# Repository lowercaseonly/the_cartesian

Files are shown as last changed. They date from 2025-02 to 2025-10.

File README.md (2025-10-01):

# The Cartesian
**The Cartesian** is a modular CNC Mill built from low-cost standard parts (which can ve bought of the shelf) as well as 3D-printed connectors.

## Folder Structure

```
.
│   README.md                      # This File
│   bom.csv                        # Bill of Materials
└───3d_models                      # Hardware 3D Models
│   └───assembly                   # Compositions of Components
│   │   │   parameter.scad         # Global Assembly Parameters
│   │   │   portal_assembly.scad   # X-Axis
│   │   │   bridge_assembly.scad   # Y-Axis
│   │   │   column_assembly.scad   # Z-Axis
│   │   │   assembly.scad          # Overall Assembly
│   └───helper                     # Helper Models (Shared between different Machine Parts)
│   │   ...
│   └───components                 # Printable Component Models
│   │   ...
│   └───shells                     # off-the-shelf Component Models
│       ...
└───src                            # Source Code
```

## Mechanical Setup
The basic mechnical structure of the described hardware consists of three linear axis which are oriented orthogonal to each other (hence the project name).

### General Considerations
The hardware is based on standard parts around which customized connectors are built. The exact bill of materials can be found in a dedicated file in the root directory of this repository and includes:

 - `NUT8` aluminum profiles (more about [T-Slot structural Framing](https://en.wikipedia.org/wiki/T-slot_structural_framing))
 - `M5` screws and nuts (more about [metric screws](https://en.wikipedia.org/wiki/ISO_metric_screw_thread))
 - `HGH20` linear guide blocks and rails (more about [HIWIN](https://www.hiwin.tw/))
 - `NEMA 23` stepper motors (more about the [NEMA](https://www.nema.org/Standards/view/Motion-Position-Control-Motors-Controls-and-Feedback-Devices) Standard)

### Design Principles
The hardware of this project is designed adhering to some basic principles:

 - The 3D Models are given as [OpenSCAD](https://openscad.org/) Files
 - All numerical values in the 3D model files are given in [mm](https://en.wikipedia.org/wiki/Millimetre)
 - Parametrization is used whenever possible. For example, the exact printing area can be specified by three individual parameters
 - A [tagging function](./3d_models/helper/bom.scad) is used in all component functions to generate the bill of material automatically

### Overall Assembly
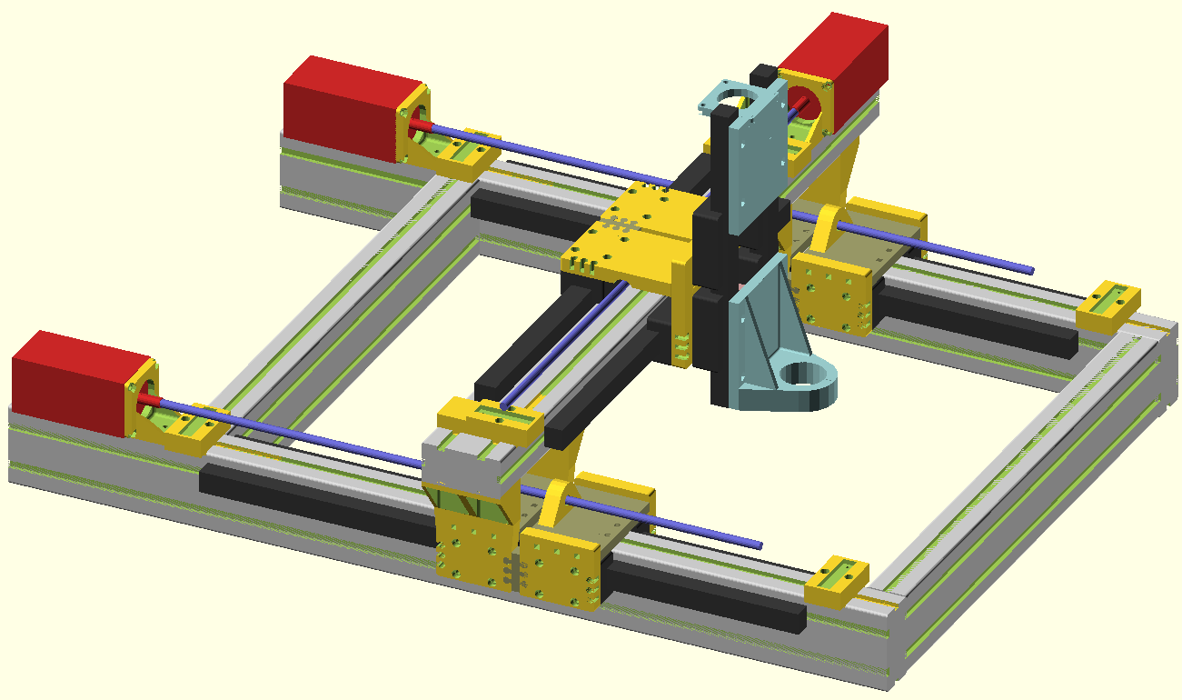
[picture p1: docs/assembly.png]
Overall Assembly

In order to validate the designs of individual components as well as for simulation and illustration purposes, the assembly of the overall machine has been created aggregating the models of individual (printable and off-the-shelf) components. All assembly files can be found in the [3d_models/assembly](./3d_models/assembly) folder. More precisely:

 - The overall [assembly.scad](./3d_models/assembly/assembly.scad) file utilizes the individual axis assemblies by geometrically linking them (using OpenSCAD's `children()` transform).
 - The assembly parameters are stored globally in [parameter.scad](./3d_models/assembly/parameter.scad). Here, multiple aspects can be adjusted:
   - The individual axis dimensions: `SPACE_X`, `SPACE_Y`, `SPACE_Z`
   - The end effector position: `POS_X`, `POS_Y`, `POS_Z`

### The Portal (X-Axis)
The X-Axis (also referred to as `portal`) consists of the main structural, rectangular frame build from T-slotted (aluminum) profiles. On this frame, two pairs of linear guide rails are mounted which commonly carry another T-slotted profile (the bridge). Each pair of guide rails is driven by a dedicated motor.

### The Bridge (Y-Axis)
The Y-Axis (also referred to as `bridge`) consists of a one T-slotted profile on which two two linear guild rails are mounted. The bridge is driven by one motor which is mounted to two T-Slots.

### The Column (Z-Axis)
The Z-Axis (also referred to as `column`) consists of a plate, mounted to two linear guide rails that carries the end-effector.

## License
The content of this repository is licensed under the terms of the `MIT license`.

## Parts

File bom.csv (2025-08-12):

BOM Level | Description | Part Number | Unit Cost | Quantity | Total Cost
 | T-Slot Profile [Type Nut8, 40x2, length: 1200mm] |  |  | 2
 | T-Nut |  |  | 20
 | Profile Angle |  |  | 20
 | M-Skrew

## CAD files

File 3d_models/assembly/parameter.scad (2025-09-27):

/*
  Author: Johannes Bayer, 2025
  License: MIT
  Description: Global Assembly Parameters
*/


REINFORCEMENT = true;
PORTAL_SPACING = 8;
BRIDGE_SPACING = 7;
COLUMN_SPACING = 10;

MOTOR_SPACE=200;

// Printing Area
SPACE_X = 600;
SPACE_Y = 600;
SPACE_Z = 300;
PORTAL_HEIGHT = 110; // TODO resolve by SPACE_Z based Formula

// Printer Head Position
POS_X = 250;
POS_Y = 200;
POS_Z = 100; // 110/300: [65-135]

// Counter Axis (Slider/Profile/Component) Dimensions
OFFSET_Y = 90;

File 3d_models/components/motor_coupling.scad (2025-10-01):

include <../helper/bom.scad>

include <../shells/motor.scad>
include <../shells/threaded_rod.scad>



MOTOR_COUPLING_DIA = 20;
MOTOR_COUPLING_LEN = 20;
MOTOR_COUPLING_ROD_ATTACH = 10.0;
MOTOR_COUPLING_SHAFT_ATTACH = 5.0;



module motor_coupling(){

    bom_item("MOTOR_COUPLING");

    difference(){

        translate([0,0,-MOTOR_COUPLING_SHAFT_ATTACH])
            cylinder(h=MOTOR_COUPLING_LEN,d=MOTOR_COUPLING_DIA);

        union(){

            translate([0,0,-MOTOR_SHAFT_LEN-MOTOR_CON_LEN])
                motor_shaft();
            translate([0,0,MOTOR_COUPLING_LEN-MOTOR_COUPLING_SHAFT_ATTACH
                           -MOTOR_COUPLING_ROD_ATTACH+NOTHING])
                cylinder(h=MOTOR_COUPLING_ROD_ATTACH, d=THEADED_ROD_DIA_OUTER);

        }

    }

    translate([0,0,MOTOR_COUPLING_LEN-MOTOR_COUPLING_SHAFT_ATTACH
                   -MOTOR_COUPLING_ROD_ATTACH+NOTHING])
        children();

}


motor_coupling($fn=400);

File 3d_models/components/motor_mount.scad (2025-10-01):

include <../helper/bom.scad>
include <../helper/motor_flange.scad>
include <../helper/t_slot.scad>


MOTOR_MOUNT_THICKNESS = 25.0;
MOTOR_MOUNT_LENGTH = 5.0;
MOTOR_MOUNT_LEFT = true;



module motor_mount(double_t_slot=false){

    bom_item("MOTOR_MOUNT",
             "T-SLOT_TYPE",double_t_slot?"double":"single");

    translate([0,0,MOTOR_FLANGE_HEIGHT/2])
        rotate([90,0,180])
            motor_flange()
                children();

    difference(){
        translate([SLOT_PROF_HEIGHT/2
                   +(double_t_slot&&MOTOR_MOUNT_LEFT?SLOT_DIST+SLOT_WIDTH:0),0,0])
            rotate([-90,90,0])
                NUT8_mount(length=MOTOR_MOUNT_THICKNESS,
                           thickness_length=MOTOR_MOUNT_LENGTH,
                           thickness_height=MOTOR_FLANGE_THICKNESS,
                           double_size=double_t_slot);
        translate([0,0,MOTOR_FLANGE_HEIGHT/2])
            rotate([90,0,180])
                motor_flange_cutout();
    };

}

motor_mount($fn=100, double_t_slot=false);

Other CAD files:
3d_models/helper/motor_flange.scad
3d_models/assembly/assembly.scad
3d_models/assembly/bridge_assembly.scad
3d_models/assembly/column_assembly.scad
3d_models/assembly/portal_assembly.scad
3d_models/components/bearing_mount.scad
3d_models/components/bridge.scad
3d_models/components/bridge_compact.scad
3d_models/components/bridge_connector.scad
3d_models/components/bridge_reinforcement.scad
3d_models/components/column.scad
3d_models/components/column_connector.scad
3d_models/components/nut_mount.scad
3d_models/components/portal.scad
3d_models/components/portal_reinforcement.scad
3d_models/components/thread_nut_mount.scad
3d_models/components/wagon_connector.scad
3d_models/helper/base_plate.scad
3d_models/helper/bom.scad
3d_models/helper/connector_a.scad
3d_models/helper/linear_wagon.scad
3d_models/helper/nut_mount_connector.scad
3d_models/helper/pillow_block.scad
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

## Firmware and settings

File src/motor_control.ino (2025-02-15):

int counter = 0;

void setup() {
  // put your setup code here, to run once:
  DDRD = 0b11111111;
  counter = 0;
}

void loop() {
  // put your main code here, to run repeatedly:

  delay(1);
  PORTD |= 0b00000001;
  delay(1);
  PORTD &= 0b11111110;
  counter++;

  if (counter%500==0)
    PORTD |= 0b00000010;
  if (counter%1000==0)
    PORTD &= 0b11111101;

}

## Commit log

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2025-06-08 Added First Draft of Linear Wagon Adapter for Portal
    [portal.scad]
2025-07-12 Added Connector to Portal
    [portal.scad]
2025-07-19 Added NUT8_45x2 Prototype Model
    [portal.scad]
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2025-07-21 Added T-Slot Profile connector
    [portal.scad]
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2025-07-22 Corrected Nut8 Mount Extrusion height
    [portal.scad]
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2025-07-22 Cleaned up Module Assembly
    [portal.scad]
2025-07-22 Corrected T-Slot Profile Parameters
    [portal.scad]
2025-07-22 Added Spindle Connector to Bridge
    [portal.scad]
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2025-07-22 Shrinked T-Slut Support to save Space and Material
    [portal.scad]
2025-07-22 Increased Circle Detail Rendering Parameter
    [portal.scad]
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2025-07-26 Fine-Tuned M-Skrew Drill Hole Sizes
    [portal.scad]
2025-08-02 Added Motor Flange Dimensions to Prepare Mount
    [motor_mount.scad]
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2025-08-02 Moved base_plate() Helper Function to Dedicated File
    [base_plate.scad, portal.scad]
2025-08-02 Moved m_skrew() Helper Function to Dedicated File
    [m_skrew.scad, portal.scad]
2025-08-02 Fixed Skrew Model Import
    [m_skrew.scad, portal.scad]
2025-08-02 Added Fist Version of motor_flange()
    [motor_mount.scad]
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2025-08-07 Moved Linear Wagon Helper Function to Dedicated File
    [linear_wagon.scad, portal.scad]
2025-08-07 Fixed Import in Motor Mount
    [motor_mount.scad]
2025-08-07 Fixed Import Structure in 3D Models
    [linear_wagon.scad, portal.scad]
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2025-08-10 Added and Improved Header Documentation in Helper Models
    [connector_a.scad, linear_wagon.scad]
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2025-08-10 Avoided Numerical Issues in NUT8_mount_complete()
    [t_slot.scad]
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2025-08-10 Reworked Parameters in NUT8_mount_complete() and NUT8_mount()
    [t_slot.scad]
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2025-08-11 Corrected Hole-Edge Distance in Motor Mount
    [motor_mount.scad]
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2025-08-12 Moved and Renamed Spindle Connector -> Nut Mount Connector to Dedicated Helper File
    [nut_mount_connector.scad, portal.scad]
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2025-08-12 Added Portal Reinforcement Component
    [portal_reinforcement.scad]
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2025-08-13 Addedd top, bottom, left, right Parameters to HGH20CA_screws()
    [linear_wagon.scad]
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2025-08-27 Clipped Nut Connector Mount as Makeshift to fit Small Printing Area in
    [nut_mount.scad]
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2025-08-27 Optimized Default Value of length Parameter in m_skrew_eject()
    [m_skrew.scad]
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2025-08-28 Fine-Tuned Tolerances in Nut Mount
    [nut_mount.scad, nut_mount_connector.scad]
2025-08-28 Fixed Wagon-Wagon Alignment in bridge_mount()
    [bridge_mount.scad]
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2025-08-31 Fixed m_nut()
    [m_skrew.scad]
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2025-09-01 Flipped Motor Flange in Motor Mount
    [motor_mount.scad]
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2025-09-01 Utilized motor_flange_cutout() in Motor Mount for Improved Nut Fitting
    [motor_mount.scad]
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2025-09-02 45 Degree Angle of Nut Holes in Motor Flange
    [motor_flange.scad]
2025-09-04 Fully Parameterized NUT8_mount() by introducing dedicated, independent Thicknesses
    [t_slot.scad]
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2025-09-07 Renamed bridge() -> intermediate() to Avoid Naming Ambiguities
    [portal.scad]
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2025-09-08 Replaced Redundant PORTAL_SPACING Parameter by Calculation
    [portal.scad]
2025-09-08 First Version of Bridge Reinforcement
    [bridge_reinforcement.scad]
2025-09-08 Properly Parameterized Nut Mount Connector in Bridge Reinforcement
    [bridge_reinforcement.scad]
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2025-09-08 Adapted Motor Mount to new T-Slot Mount Definition
    [motor_mount.scad]
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2025-09-09 Added Crossbars and Prepared Base Frame for Motor Mount
    [assembly.scad]
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2025-09-09 Added Reinforcement Option to Bridge Core
    [bridge.scad]
2025-09-09 Added Bridge Reinforcement to Assembly
    [assembly.scad]
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2025-09-09 Added Portal Reinforcement to Assembly
    [assembly.scad]
2025-09-10 Shortened Bridge to fit Small Printing Area
    [bridge.scad]
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2025-09-10 Moved set Arc Segment Variable from Global Definition to Main Function Call in all Components
    [bridge.scad, bridge_reinforcement.scad, motor_mount.scad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]
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2025-09-12 Added Default Value to extend Parameter in m_skrew()
    [m_skrew.scad]
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2025-09-12 Applied MOTOR_SPACE Variable to Bridge T-Slot Profile in Assembl
    [assembly.scad]
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2025-09-13 Replaced effector_mount() by pillow_block() Utilization in Column
    [column.scad]
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2025-09-14 Added Plane Crop to pillow_block() to Support center_dist Values Smaller than diameter and wall thickness sum
    [pillow_block.scad]
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2025-09-16 Added Functionality for Generating the Bill of Material Automatically
    [assembly.scad, bearing_mount.scad, bom.scad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]
2025-09-16 Added linear_slider() module combining HGH20() and HGH20CA() with coordinate Transform
    [linear_wagon.scad]
2025-09-16 Moved to Main Module Call in Nut Mount
    [nut_mount.scad]
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2025-09-16 Added Bridge Motor and Motor Mount to Assembly
    [assembly.scad]
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2025-09-17 Cleanup and Introduction of OFFSET_Y Parameter and Double T-Slot Bearing Mounts for Bridge in Assembly
    [assembly.scad]
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2025-09-17 Increased Safety Margin of Bearing Mount in Column
    [column.scad]
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2025-09-18 Redefined Linear Wagon and Slider to Center at Origin
    [linear_wagon.scad]
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2025-09-18 Adapted Motor Flange to new Base Plate Definition
    [motor_flange.scad]
2025-09-18 Adapted Motor Mount to Definition of Motor Flange
    [motor_mount.scad]
2025-09-18 Fixed overhang in HGH20CA_plate()
    [linear_wagon.scad]
2025-09-18 Adapted Portal Reinforcement to new Base Plate Definition
    [portal_reinforcement.scad]
2025-09-19 Adapted Bridge Reinforcement to new Base Plate Definition
    [bridge.scad]
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2025-09-19 Added Portal Reinforcement Symmetrically to Assembly
    [assembly.scad]
2025-09-19 Added Bridge including Reinforcement Symmetrically to Assembly
    [assembly.scad]
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2025-09-19 Parametrization and Adaptation to new Wagon Connector Definition in Assembly
    [assembly.scad]
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2025-09-19 Introduced invert Flag in linear_slider()
    [linear_wagon.scad]
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2025-09-19 Renamed NUT8_mount_base() -> support_base() and Moved to Dedicated File
    [support.scad, t_slot.scad]
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2025-09-19 Fixed Couout Alignment in support()
    [support.scad]
2025-09-19 Re-Implemented Column Support Structure to Avoid Numerical Issues
    [column.scad]
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2025-09-20 Renamed column() -> column_lower() and Encapsulated Overall column() Function
    [column.scad]
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2025-09-20 Introduced Margins to Fix Rendering for Zero-Thick Base in Support Structure
    [support.scad]
2025-09-20 Simplified Column Code by Applying Support Structure Fix
    [column.scad]
2025-09-20 Added Support Structure to Bearing Mount in Column
    [column.scad]
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2025-09-21 Aligned Nut Mount with Connector Base in Colomn Connector
    [column_connector.scad]
2025-09-21 Corrected Nut Length in Column Mount
    [column_connector.scad]
2025-09-21 Added Fitting Marging to Nut Mount in Column Connector
    [column_connector.scad]
2025-09-21 Decreased Column Connector Height to Avoid Collision with Main Column
    [column_connector.scad]
2025-09-21 Decreased Column Connector Width to Avoid Collision with Column Sliders
    [column_connector.scad]
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2025-09-21 Finetunig in Column Bearing Mount Support to Avoid Collision with Linear Sliders
    [column.scad]
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2025-09-22 Fixed Column Connector Position in Assembly
    [assembly.scad]
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2025-09-24 Fixed Children Transform in Bridge
    [bridge.scad]
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2025-09-25 Moved portal_assembly(), bridge_assembly() and column_assembly() to Dedicated Files
    [assembly.scad, bridge_assembly.scad, column_assembly.scad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]
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2025-09-25 Fixed Overall Assembly File
    [assembly.scad]
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2025-09-25 Replaced Redundant Union Operators
    [column.scad, connector_a.scad, motor_flange.scad]
2025-09-25 Added Missing Nut Mount Instances to Portal
    [portal_assembly.scad]
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2025-09-26 Adapted Portal Assembly to new Nut Mount Alignment
    [portal_assembly.scad]
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2025-09-27 Replaced Usage of motor() with motor_shaft() in motor_coupling()
    [motor_coupling.scad]
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2025-09-27 Fixed Parameters in Motor Coupling
    [motor_coupling.scad]
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2025-09-27 Fixed Cildren Transform in Motor Coupling
    [motor_coupling.scad]
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2025-09-27 Shortened Motor Coupling
    [motor_coupling.scad]
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2025-09-27 Decreased Outer Diameter in Motor Coupling to fit into Tight Mounting Space
    [motor_coupling.scad]
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2025-09-28 Added Brdige Connector and Nut Mount to Bridge Assembly
    [bridge_assembly.scad]
2025-09-28 Finetuning in Bridge Reinforcement
    [bridge_reinforcement.scad]
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2025-09-30 Added Motor Flange Support Structure to Upper Column Plate
    [column.scad]
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2025-09-30 Utilized Motor Flange Children Transform in Motor Mount
    [motor_mount.scad]
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2025-10-01 Increased Distance between Motor Mount and Bearing Mount in Upper Column
    [column.scad]
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2025-10-01 Fixed Children Transform in T-Slot Model
    [t_slot.scad]
2025-10-01 Updated Portal and Portal Imports WRT new T-Slot Model Location
    [portal.scad, portal_assembly.scad]
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2025-10-01 Updated Bridge Assembly Imports WRT new T-Slot Model Location
    [bridge_assembly.scad]
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2025-10-02 Added Header and BOM Tagging to Linear Slider
    [linear_slider.scad]
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2025-10-03 Re-Applied Correct Translation to Portal Slider and Cleanup in portal_assembly()
    [portal_assembly.scad]
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2025-10-03 Fixed Children Invokation in Portal Assembly
    [portal_assembly.scad]
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
